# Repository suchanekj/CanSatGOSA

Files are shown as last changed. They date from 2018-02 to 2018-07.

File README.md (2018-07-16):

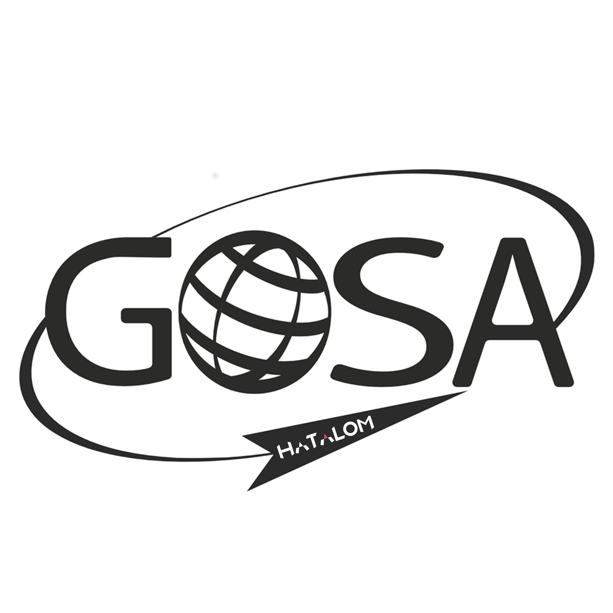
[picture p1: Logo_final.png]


# About
CanSat code is software for autonomous exploration and landings of probe "CanSat" developed by Gymnazium Opatov Space Agency especially by Jakub Suchánek.

The whole code is using following subcodes:
* GroundStation - incoming datas of pressure, position, time and temperature
* Cansat (2.0) - used libraries - Code, Cirtuits...
* Final report (Detail information about the probe Cansat in LaTex article. Unfortunately only in Czech.)
* Pre launch report - English detail description of Cansat 2.0
* Analysis - our own atmospheric model running on data from CanSat
* After flight report - final description of the whole project

# Support
In case you need help with use of our program or support us, you can contact us on our public email dotazy@gosa.cz or on email of programming director suchanek989@seznam.cz

# Contributing

Contributions are welcome and encouraged.  You can contribute in many ways:

* Documentation updates and corrections.
* How-To guides - received help? Help others!
* Bug reporting & fixes.
* New feature ideas & suggestions.

# Requirements
* Hardware requirements: qbcan for matching ports or an AVR microcontroller with RFM69HW (will have to edit port specifications)
* Idealy used for original construction of CanSat: https://github.com/suchanekj/CanSatGOSA/tree/master/Schematics
* Also used for original construction of CanSat 2.0: https://github.com/suchanekj/CanSatGOSA/tree/master/CanSat2.0/Schematics 
* Software requirements: AVR chip programmmer

# Used code
* Uses the RFM69 Library from: Feix Rusu (2014), felix@lowpowerlab.com http://lowpowerlab.com/
* Inspired by qbcan library and hardware http://doc.open-cosmos.com/Qbcan_modular

# Open Source / Contributors
CanSat software that is **open source** and is available free of charge without warranty to all users.

Current contributors:
* Suchánek, Jakub (suchanekj)
* Novotný, Patrik  (PatriktheAstronomer)
* Vítek, Martin (MArtytraM99)
* Zeman, Jakub (Jakubzmn)
* Völfl, Lukáš (LukasVolfl)
# Versions:
* 1.0 Groundstation subcode created and README added 29/03/2018
* 1.1 CanSat subcode created and Model files completed 01/04/2018
* 1.2 Final report (LaTex article) created 03/04/2018
* 1.3 Final report (LaTex article) completed 12/04/2018
* 2.0 New contributers, Analysis, CanSat 2.0 3D printed parts and PLR.pdf (Pre-launch report) added 18/06/2018
* 2.1 Analysis part 2 completed, chamber software added 28/06/2018
* 2.2 After flight report added, Analysis repaired and added - project completely done 16/07/2018
 (**Thanks everyone for your support to our project!**)

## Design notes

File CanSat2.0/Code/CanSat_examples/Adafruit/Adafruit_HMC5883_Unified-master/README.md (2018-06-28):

#Adafruit HMC5883L Driver (3-Axis Magnetometer) #

This driver is for the Adafruit HMC5883L Breakout (http://www.adafruit.com/products/1746), and is based on Adafruit's Unified Sensor Library (Adafruit_Sensor).

## About the HMC5883 ##

The HMC5883L is a digital (I2C) compass (magnetometer).  The magnetometer measure magnetic force, which is useful to detect magnetic north.

More information on the HMC5883L can be found in the datasheet: http://www.adafruit.com/datasheets/HMC5883L_3-Axis_Digital_Compass_IC.pdf

## What is the Adafruit Unified Sensor Library? ##

The Adafruit Unified Sensor Library (**Adafruit_Sensor**) provides a common interface and data type for any supported sensor.  It defines some basic information about the sensor (sensor limits, etc.), and returns standard SI units of a specific type and scale for each supported sensor type.

It provides a simple abstraction layer between your application and the actual sensor HW, allowing you to drop in any comparable sensor with only one or two lines of code to change in your project (essentially the constructor since the functions to read sensor data and get information about the sensor are defined in the base Adafruit_Sensor class).

This is imporant useful for two reasons:

1.) You can use the data right away because it's already converted to SI units that you understand and can compare, rather than meaningless values like 0..1023.

2.) Because SI units are standardised in the sensor library, you can also do quick sanity checks working with new sensors, or drop in any comparable sensor if you need better sensitivity or if a lower cost unit becomes available, etc. 

Light sensors will always report units in lux, gyroscopes will always report units in rad/s, etc. ... freeing you up to focus on the data, rather than digging through the datasheet to understand what the sensor's raw numbers really mean.

## About this Driver ##

Adafruit invests time and resources providing this open source code.  Please support Adafruit and open-source hardware by purchasing products from Adafruit!

Written by Kevin (KTOWN) Townsend for Adafruit Industries.

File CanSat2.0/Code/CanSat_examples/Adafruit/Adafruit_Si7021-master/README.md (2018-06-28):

Adafruit Si7021
===============

Driver for Adafruit's Si7021 humidity / temp sensor breakout

Designed specifically to work with the Si7021 breakout in the adafruit shop

   * https://www.adafruit.com/products/3251

This chip uses I2C to communicate, 2 pins are required to interface

Adafruit invests time and resources providing this open source code, 
please support Adafruit and open-source hardware by purchasing 
products from Adafruit!

Check out the links above for our tutorials and wiring diagrams 

Written by Limor Fried/Ladyada for Adafruit Industries.  
BSD license, all text above must be included in any redistribution

To download. click the ZIP button on the right, rename the uncompressed folder Adafruit_Si7021. Check that the Adafruit_Si7021 folder contains Adafruit_Si7021.cpp and Adafruit_Si7021.h

Place the Adafruit_Si7021 library folder your arduinosketchfolder/libraries/ folder. You may need to create the libraries subfolder if its your first library. Restart the IDE.

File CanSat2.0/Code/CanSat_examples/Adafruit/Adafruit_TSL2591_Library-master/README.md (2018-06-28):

# Adafruit TSL2591 Library 



This is an Arduino library for the TSL2591 digital luminosity (light) sensors. 

Pick one up at http://www.adafruit.com/products/1980

You'll also need the Adafruit_Sensor library from https://github.com/adafruit/Adafruit_Sensor

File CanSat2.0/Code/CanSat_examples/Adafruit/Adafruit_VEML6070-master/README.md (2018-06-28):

# Adafruit VEML6070 Library 



This is a library for the Adafruit VEML6070 UV sensor breakout:
  * https://www.adafruit.com/products/2899
 
Check out the links above for our tutorials and wiring diagrams. This chip uses I2C to communicate

Adafruit invests time and resources providing this open source code, please support Adafruit and open-source hardware by purchasing products from Adafruit!

Written by Limor Fried/Ladyada for Adafruit Industries.
MIT license, all text above must be included in any redistribution

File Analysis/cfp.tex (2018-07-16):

%Jak dělat reference:
% \cite{baker}

%Jak dělat poznámky:
% \footnote{tralala}

% TO DO
% Některá vysvětlení rovnic mohou být málo srozumitelná, chtělo by to víc se rozepsat (hlavně při úrovni pana grafa (který podle mě je fyzik mezi porotci))
% přidat pod rovnice popis proměných
% ohybani svetla vysvetlit, prepocitavani namerenych spektro hodnot taky, jeste absolute humidity

%
\documentclass{cfp}  

%
\usepackage[utf8]{inputenc}
\usepackage{chngcntr}
% \usepackage[margin=1in,includeheadfoot,headheight=13.6pt,footskip=2cm]{geometry}
\usepackage{amsmath}
\usepackage{pgfplots}
\usepackage{listingsutf8}
\usepackage{graphicx}
\usepackage{amsfonts}
\usepackage{txfonts}
\usepackage[colorlinks=true,urlcolor=blue]{hyperref}
\usepackage{eurosym}
\usepackage{chemfig}
\usepackage[version=4]{mhchem}
\usepackage{multicol}
\usepackage[symbol*]{footmisc}
\usepackage{indentfirst}
\usepackage{mathtools}
\usepackage{fixltx2e}
\usepackage{siunitx}
% \usepackage{titlesec}
% \usepackage{float}
% \usepackage{fancyhdr}
% \usepackage{array}
% \usepackage{longtable}
% \usepackage{dirtytalk}
\pdfminorversion=5 
\pdfcompresslevel=9
\pdfobjcompresslevel=2

\counterwithin{figure}{section}
\counterwithin{equation}{section}
\renewcommand{\thefootnote}{\fnsymbol{footnote}}
\setlength{\parindent}{3ex}
\setlength{\parskip}{0ex}
\newcommand{\rpm}{\sbox0{$1$}\sbox2{$\scriptstyle\pm$}
  \raise\dimexpr(\ht0-\ht2)/2\relax\box2 }
\newcommand{\degree}{^{\circ}}
\begin{document} 

   \title{CFP-18-Hatalom}

   \subtitle{ Simulation of finding life and life supporting conditions on exoplanets }

   \author{J. Suchánek
   		  \inst{1}
		  \and          
          P. Novotný
   		  \inst{2}
   		  \and
   		  J. Janoušek
   		  \inst{3}
   		  \and
   		  Lukáš Völfl
   		  \inst{4}
   		  \and
   		  Martin Vítek
   		  \inst{5}
   		  \and
   		  Jakub Zeman
   		  \inst{6}
          }
          
   \institute{Gymnázium Opatov, Czech Republic\\
              \email{suchanek989@seznam.cz}
         \and
             Gymnázium Opatov, Czech Republic\\
             \email{patrik.novotny.jes@seznam.cz}
         \and
             Gymnázium Opatov, Czech Republic\\
             \email{honza.janousek.11@gmail.com}
         \and
             Gymnázium Opatov, Czech Republic\\
             \email{luky.volfl@gmail.com}
         \and
             Gymnázium Opatov, Czech Republic\\
             \email{martulavitek@seznam.cz}
         \and
             Gymnázium Opatov, Czech Republic\\
             \email{kubazeman@volny.cz}
             }

   \date{July 15, 2018}

% \abstract{}{}{}{}{}
 
  \abstract
  % context heading (optional)
  % {} leave it empty if necessary  
   {Our analysis, like our mission, deals with the detection of life and the conditions necessary for its creation and development.}
  % aims heading (mandatory)
   {This work aims to introduce the analysis of the data we made after the flight of our Cansat and partly our entire project.}
  % methods heading (mandatory)
   {We conducted two types of analysis, biological analysis, and calculations of other variables using our own models that we developed. These are approximation models that are all available on our Git. This document also serves as their documentation.}
  % results heading (mandatory)
   {Tested planet seems habitable and even contains both microscopic and macroscopic life identical in basic structure to the life on Earth.}
  % conclusions heading (optional), leave it empty if necessary 
   {The analysis was thorough enough to declare with near certainty that it is habitable for humans. The project has had some failures but the analysis has turned out correct.}

   \keywords{Cansat, Gram's staining, Greenhouse effect, Exoplanet properties, Kepler 62, Atmospheric spectroscopy}

   \maketitle
%
%________________________________________________________________

\section{Introduction}
\par Our vision of Cansat was to build an interplanetary probe, which should not take care of the process of getting to a planet but the landing. We are landing at another planet. The one we selected is a planet orbiting around star named Kepler 62. It cannot be seen by an eye from Earth and its radius is smaller than radius of our Sun. Kepler 62 is situated in Lyra constellation and it is nearly 1,200 light years away from the Solar System. There are 5 planets orbiting around Kepler 62. Two of them, “e” and “f”, are very interesting for us as they lay in the habitable zone.
\par Planet “e” lies on the inner side of the habitable zone. According to calculations made using its semi-major axis, it is too hot for the possibility of existence of life similarly to Venus. However, its sibling Kepler 62f is much more promising. We do not have every piece of data, but we know that in the given orbital distance from the Kepler 62, the planet should have temperature of -40$^\circ$C. However, if it had 5 times thicker atmosphere composed of CO\textsubscript{2}, which is not anything uncommon, liquid water could be present on the surface of the planet. Kepler 62 is a stable star with low mass and metallicity compared to the Sun. It should shine twice as long than what is the age of the universe.
\par The whole system is up to 2 billion years older than our system. The planet probably has its own moon and an inclined rotational axis, therefore seasons change while orbiting its parent star. From all this data, we can assume that there is not any better candidate for finding extraterrestrial life. We can estimate lower stage of evolution according to the fact that we are not receiving any data transmission from the Kepler 62 system.
\par As the planet has thick atmosphere, controlled landing is possible. We have decided for drone-like landing with 4 rotors. Our aim is to land in a pre-determined spot, where our Cansat takes sample of the soil from the ground. Then we post-analyse the sample in our decontamination chamber which we had made ourselves.
\par Of course, it is necessary to realise that the whole mission was actually a simulation on Earth, so the expected outcome is whether we can prove that the Earth is habitable and inhabited and compare our measured and calculated data to the real ones to prove the functionality of our Cansat. However, some outputs are calculated also as on Kepler 62f.
\begin{figure}[!h]
\centering
\caption{Diagram showing the Kepler 62 system}
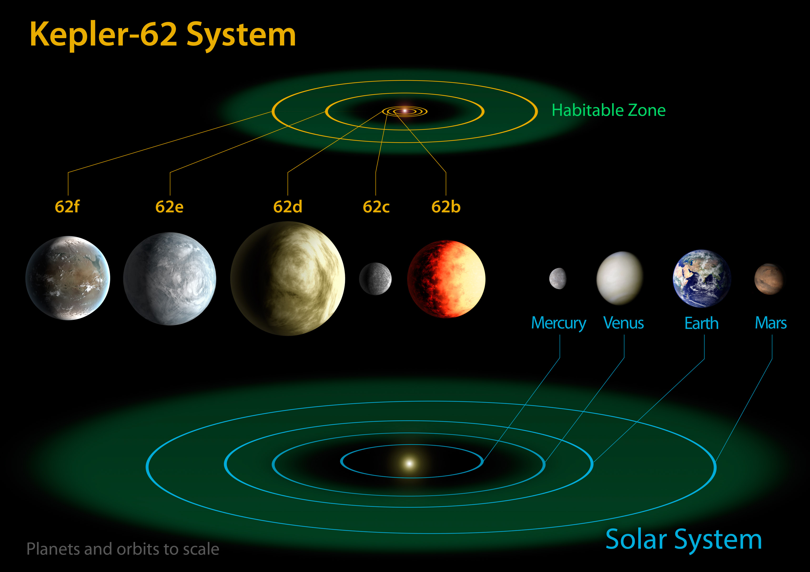
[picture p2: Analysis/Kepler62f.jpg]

\end{figure}
\section{Project description}
\par Our objective was to simulate a sample retrieval mission to a potentially habitable exoplanet, where a sample of soil is taken as well as a video and numerous data assessing the probability of Earth-like life existing on the planet.
\par The main goal was to detect life and conditions for it such as concentration of various gases. Those achievements are necessary for the launch to be considered successful. Other goals were to land the Cansat in a predefined location and to broadcast live data and video to our websites. \cite{Websites}
\par Our task was not easy and we have been aware of that since beginning of the project. We knew that not all of the parts will work but we were prepared for that. Our strategy was to fill as much as we could with sensors and other electronic devices so that in case of one sensors failure we would still get a lot of data to be processed. Unfortunately, before the final flight unexpected problems occurred and we did not have enough time to fix them. The most of hardware was working fine, however, because of few substantial mistakes our Cansat did not work at all. These issues and other information about construction are described in following paragraphs.
\subsection{Cansat}
\subsubsection{Materials and structural design}
\par The main structural body consists of 6 hull parts, which are 3D printed and is screwed to each other. The hull is round at the top and consists of four pillars in the remaining space. Four arms made out of carbon rod are attached to the top part in such way that they can easily move themselves into horizontal position. At the ends of the arms there are printed motor holders for secure and tight fit. In the pillars there are 16 batteries providing the whole Cansat with enough power for the flight and measurements.
\par The space inside was filled with various electronic parts. On the top, there is a three-part main circuit board, which is the “brain” of whole Cansat and on which most of sensors are placed. In the lower inside area there is a flight controller, a power regulator, a servo for soil sample and camera which broadcasts the whole flight to the ground station. All of these parts were  connected to a vertical PCB interconnecting everything and attaching it to the main PCB.
\par According to our plan GSM module should be sited near the flight controller for receiving other data. However, we are convinced that using GSM does not make any sense with our mission, landing on exoplanet.
\begin{figure}[!h]
\centering
\caption{Block diagram}
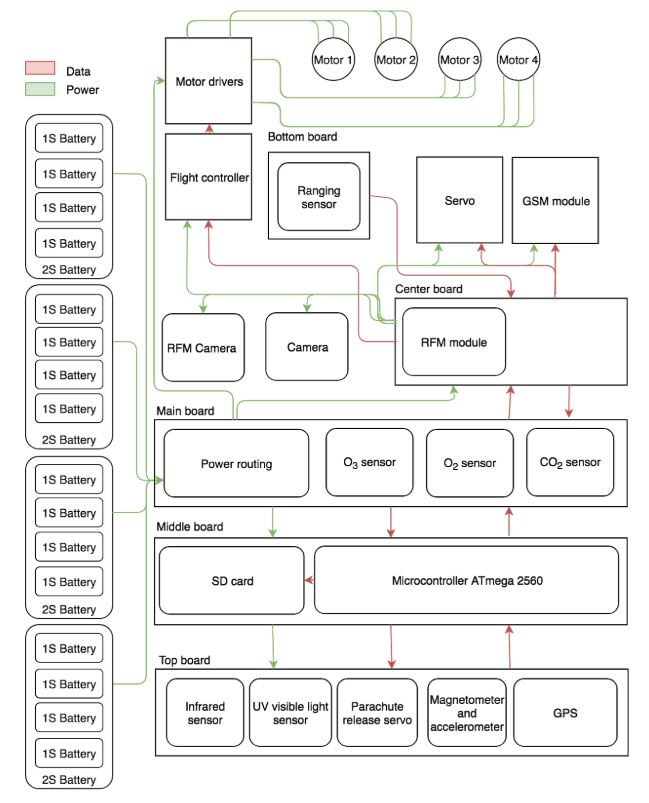
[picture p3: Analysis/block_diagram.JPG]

\end{figure}
\subsubsection{The main hardware issues}
\par During construction and testing of our Cansat there kept repeatedly occurring severe issues with I2C interface devices. The fact that all these problems always disappeared spontaneously made them very difficult to diagnose and we were not able to detect the main reasons of the occasional misbehaviour of our Cansat. All these led to the critical moment, when, despite many successful tests, the SPI and I2C interfaces stopped responding a few moments before the final launch. Due to this, we lost, among the others, also sensors (connected to I2C) measuring the altitude, velocity, acceleration and proximity, which were necessary for the autonomous drone landing system. Secondly, despite values from analogue sensors still being measured, we were unable to store or transmit any data because of not working transmitter and SD card (connected to SPI). 
\par Despite precise tests and measurements after the launch, such as connecting every single sensor separately to the Arduino and checking it or searching for any possible shorts, we could not identify the concrete issue.
\par The most probable explanation is a short between mentioned interfaces which was caused by a metal fragment from cutting PCBs or a thin piece of wire fallen in the circuit. This theory is also supported by the fact that there were found a few metal fragments in drone motors.
\par According to mentioned information, the main reason is in general the insufficient precision during the manipulation with Cansat and avoiding impurities.
\subsubsection{Recovery system}
\par The descent should have been controlled using 4 electric motors which combined have about 640 g of thrust at max. We had planned that arms holding the motors put themselves from resting position into flight position. This system was tested three months before the final competition with receiver placed in Cansat, which was connected to transmitter controlled by a person. The test was successful and Cansat was able to fly with someone’s help. 
\par The stabilisation was possible thanks to flight controller F3 SP Racing, which is normally used as a main board for racing quads. It contains only an accelerometer, gyroscope and tuned software needed for communication with ESCs (Electric speed controller). All of these parts, motors as well, were made for quad racing and for this reason our satellite had enough power and a fast response.
\par After stabilisation motors should have slowed down the descent and then it would have been navigated by GPS, barometer for precise height and magnetometer. Right above ground, about 5 meters, Cansat would have slowed down even more for soft touchdown.
\par Before flight we were forced to use parachute only because of the problems mentioned above. For some reason GPS became very unreliable since we landed on Azores. From our point of view, it could be damaged during flight to Azores or during checking our luggage in. After the issues with  I2C interface the other important sensors like accelerometer and proximity sensor became non-functional. Without all these sensors we were unable to determine the exact location of our Cansat and flight with propellers was impossible.
\begin{figure}[!h]
\centering
\caption{Exploded view}
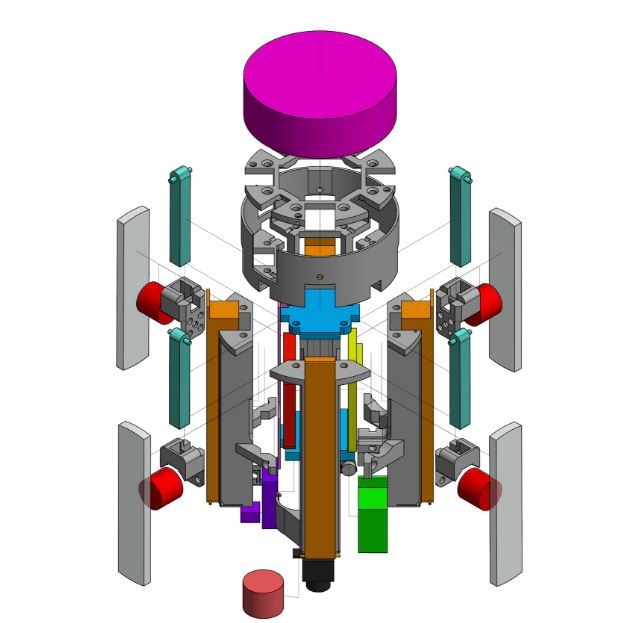
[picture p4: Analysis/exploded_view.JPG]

\end{figure}
\subsubsection{Double emergency landing system}
\par What we would like to highlight is our solution of the emergency landing. To explain our emergency system it is necessary to mention, that the logics based on ATmega and the flight-controller are two separated systems, so that any error on one of them can’t influence the other one. 
\par In case of failure of any “drone part”, such as motors, regulator or already mentioned flight-controller, the logics detect this misbehaviour (e.g. to high descend velocity), it stops the motors and releases the parachute using a small servo placed near the top board. After that the Cansat would be able to land safely. That is how our primary emergency system works.
\par The secondary emergency landing system is activated when the logics stops working. In this case the flight-controller overtakes the control of motors, sets a stable throttle for slow descending and lands, using its own embedded gyroscope.
\subsubsection{Final electrical design}
\par The CanSat contained nine custom PCBs. In the top part three parallel round PCBs were located. The top one contained sensors:
\paragraph{GPS ublox neo-m8n}This  module contains two independent parts: compass, which communicates via I2C and GPS module connected to serial port. It has also its own memory to store the last recognised location, so it can synchronise faster when initiated. It is very important sensor for autonomous landing.
\paragraph{Humidity sensor SI7021}Humidity is important factor when investigating the possibility of life. Using I2C inteface. Its precision is $\pm$ 3$\%$ RH (max), 0–80$\%$ RH
\paragraph{Light sensors TSL25911 (visible and infrared)}From observing received light in different altitudes is possible to estimate content of the atmosphere. Using I2C interface.
\paragraph{VEML6070 (ultraviolet)}UV light is dangerous for many forms of life and its measuring in different altitudes give us a chance to estimate content of the atmosphere. Using I2C interface.
\paragraph{Pressure and temperature sensor MPL3115}Combined with other data (e.g. G), pressure can be used to count the thickness of the atmosphere and the right temperature is necessary for planet’s habitability. Using I2C interface. Precision ADC resulting in 0.1 meter of effective resolution.
\paragraph{Magnetometer and accelerometer LSM303AGRTR}This sensor is essential for the autonomous landing system. Using I2C interface.
\par On the middle board there were an ATmega2560 microcontroller and a SD card. The lower board took care of power routing and regulation and also contained gas sensors:
\paragraph{MG812 (CO\textsubscript{2})}Range: 350-10000ppm CO\textsubscript{2}
\paragraph{MEO2 (O\textsubscript{2})}Range: 0-25\%vol
\paragraph{SP3-61 (O\textsubscript{3})}Range: 100ppb O\textsubscript{3}
\par Levels of these three gasses are very important when investigating the habitability of the planet, especially for atmosphere’s breathability and the greenhouse effect. Then our Cansat was equipped  with one external sensor:
\paragraph{Distance laser sensor VL53L0X}This sensor helps with soft touchdown of Cansat, because GPS and barometer are not accurate enough. Using I2C interface.
\par Batteries were connected four in parallel on each pillar PCB which have connectors for charging and connection. To the bottom of the main PCBs was connected a vertical PCB to which all modules or devices were connected. In that space motor drivers, flight controller, gamma detection board, sample collection servo, and camera were located.
\par Sixteen 1S LiPo batteries are used in a 2S (7.4V) configuration. Each battery gives 200 mAh at 3.7V and allows 35C discharge. That amounts to 1600mAh at 7.4V and 280C discharge. All logic electronics had been expected to draw up to 1A and the motors draw 15A on average. Because we decided to use only parachute we had much more energy than we had supposed. After the flight the voltage of one battery cell was at 4,1 V (maximum charge is 4,2 V). 
\par The PCBs were designed using KiCAD. All schematics are available at our GitHub/../Circuit \cite{Git-Circuit} and a detailed list of parts is located at our website. \cite{Websites}
\subsubsection{Sofware design}
\par The program initializes and then keeps running in loop where it measures data from sensors and GPS, based on GPS controls motors speed and CanSat’s direction and transmits data to ground station.
\par If any component fails, a watchdog is triggered to reset the microcontroller and the faulty component is disabled during initialization. If this happens during flight or any component required for flight is disabled the program jumps to parachute flight as a security precaution, disabling the motors and releasing the parachute. This happens within five seconds of a fault causing the program to freeze.
\par All Cansat software is written in Arduino code based on C++. We used a huge amount of libraries for which we thank their creators. We used CLion IDE, Atom editor, Arduino IDE and PDE (Processing Development Environment). Every bit of our code or code we used has GNU GPL license and it is available at our GitHub. \cite{Git - Code}
\begin{figure}[!h]
\centering
\caption{Software decision tree}
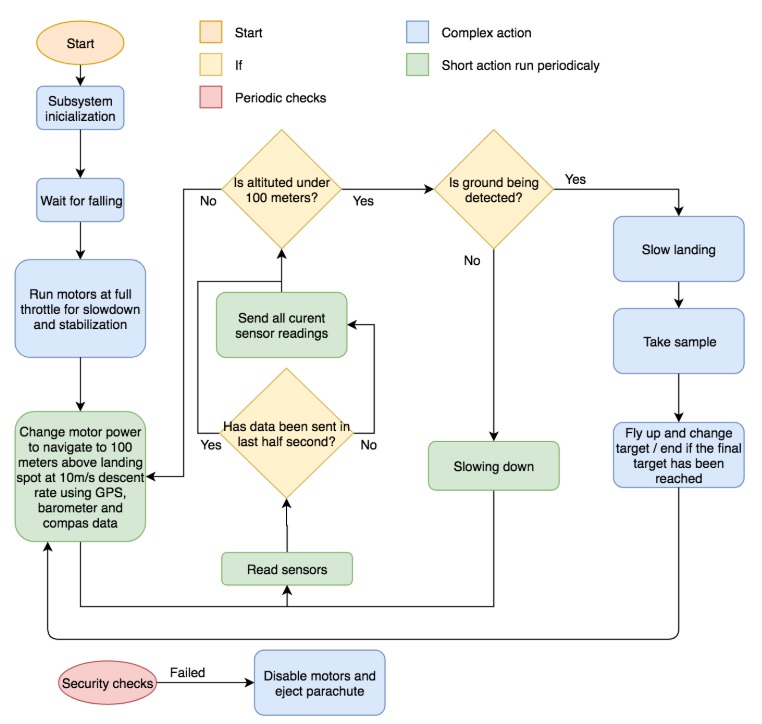
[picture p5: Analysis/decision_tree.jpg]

\end{figure}
\subsection{Ground station}
\subsubsection{Ground support equipment}
\par The ground station is split up between two laptops. One is receiving through an analogue antenna the video feed from onboard camera. The emitting power of video transmitter was approximately 200 mW and for two kilometers we needed more. However, we were limited by space in our satellite and by maximum power of batteries. For this reason, we decided to use diversity receiver with three patch antennas (14 DBI). That set should work to distance over 2,5 km. The receiving video was saved locally on the computer. We had also planned to stream the video to our Youtube channel for fans but there was no stable internet connection on the spot of the flight. 
\par The second laptop was connected to Arduino Nano via USB connection and runs a processing sketch which listened to Arduino’s serial. The sketch processes the input data, saves all communication and logs errors were capable of sending data to our web page where it is stored as a backup and graphed for live inspection. The Arduino is running a simple script for receiving data from Yagi antenna which we made ourselves and printing it to the serial.
\section{Data measurements and processing}
\subsection{Theory}
\subsubsection{Basic variables}
\paragraph{Gravitational acceleration}If we average each partial acceleration measured and calculate a Pythagorean sum of those, we should get gravitational acceleration. The problem is that the axis can not rotate during measurements. The data from a gyroscope is not reliable enough due to low sampling level. Therefore only data measured on the ground can be used.
\paragraph{Atmospheric density} The vertical gradient of pressure is linear to the density of the air:\\
\begin{equation}
    \rho = g \frac{dp}{dh}
\end{equation}
\paragraph{Atmospheric composition} \label{basic}
From Tinetti's analysis \cite{Tinetti} we obtained the general composition of the exoplanet atmosphere, depending on the variables we know or can compute:
\begin{figure}[!h]
\centering
\caption{Exoplanet composition}
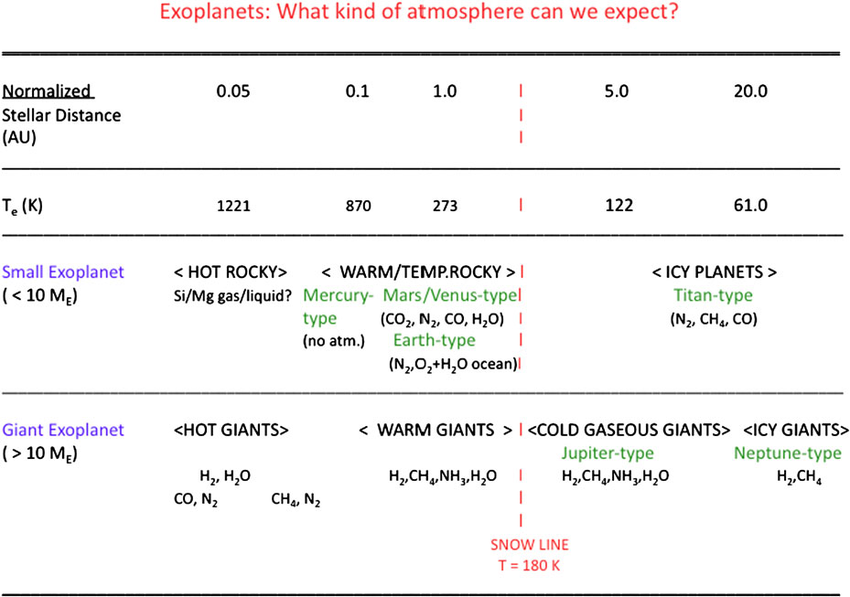
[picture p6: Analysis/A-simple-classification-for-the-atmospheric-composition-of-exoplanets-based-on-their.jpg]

\end{figure}
\paragraph{Mass of the planet} The mass of the planet can be obtained using Newton's law of gravity:\\
\begin{equation}
    M = \frac{g R^2}{G}
\end{equation}
\paragraph{Atmospheric density} The vertical gradient of pressure is linear to the density of the air:\\
\begin{equation}
    \rho = g \frac{dp}{dh}
\end{equation}
\paragraph{Average molecule mass} We can derive the number of particles per unit of volume from the ideal gas law and from that and density the molecule mass:\\
\begin{equation}
m_{molecule} = \frac{\rho}{N} = \frac{\rho k_B \tau}{p}
\end{equation}
\paragraph{Mass of the atmosphere}
From Trenberth's analysis \cite{Trenberth} we get an equation to calculate the mass of atmosphere:
\begin{equation}
m_{atm} = \frac{2\pi R^2 f}{g} \int_{-\frac{\pi}{2}}^{\frac{\pi}{2}} [p_s(\theta)]cos\theta d\theta
\end{equation}
where $f$ is the net effect of the shape of the planet and gravity variations with height and latitude but its value is very close to one and therefore at our level of precision negligible, as we cannot determine it exactly, $R$ is radius of the planet, $g$ is gravitational acceleration and $[p_s]$ is the average surface pressure. \subsubsection{Size of the atmosphere}
The two major factors limiting the size of the atmosphere, that is the altitude, at which an average molecule will escape into space, are the following:
\paragraph{Speed of molecules exceeding escape velocity} Even the top of the atmosphere rotates with the planet so the speed of some molecules is at least the sum of the rotational velocity and mean quadratic velocity of the molecules. As the velocity of molecules depends on temperature, which we did not measure a guess must be made. As there is very low density at the top of the atmosphere, the thermal conductivity can neglected. The top of the atmosphere is mostly heated by highly energetic particles from deep space (they do not originate in the star so their concentration can be considered constant in nearby stellar systems. Therefore we can say the temperature there is the same as at the top of the atmosphere of the Earth with the expected precision of a 100 kelvins (it propagates only as a small deviation).
\paragraph{Magnetosphere} We can expect form figure \ref{mag} and from Maxwell's second equation that the size of magnetosphere will be roughly linear with size and from the figure that a magnetic field at least third of the size of Earth's one will be good enough.
\begin{figure}[!h]
\centering
\caption{Earth magnetosphere under solar wind pressure}
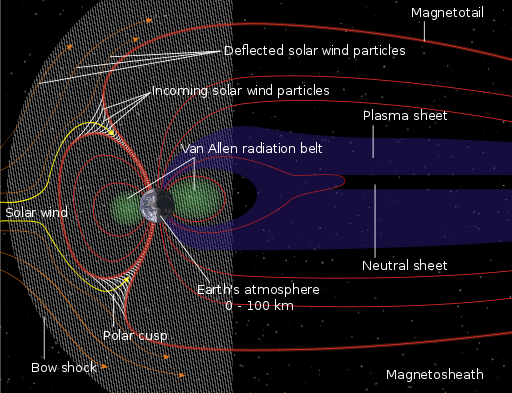
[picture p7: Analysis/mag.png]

\label{mag}
\end{figure}
\begin{align}
v_{escape} &= v_{rotational} + v_{mean quadratic}\\
\sqrt{\frac{2MG}{r}} &= \frac{2 \pi r}{T_{rotation of planet}} + \sqrt{\frac{3 k_B \tau}{m_{molecule}}}
\end{align}
\paragraph{Solar constant}
\begin{align}
P = \frac{k_B*4*\phi*r_{star}^2*T_{star}^4}{d^2*4*\phi}
\end{align}
where $k_B$ is Boltzmann's constant, $r_star$ is Parent star's radius, $T_star$ represents parent star's surface temperature in kelvins, d represents distance between the star and the place, where we measure solar constant. Basically, it is the radiance of an absolutely black body on an area of 1 $m^2$ per sphere of a given radius.
\paragraph{Temperature without greenhouse effect}
\begin{align}
T = \bigg(\frac{P}{4*k_B} * (1-A)\bigg)^{0.25}
\end{align}
where A is albedo, which is the variable that tells us what amount of light on a scale from 0 to 1 reflects the body. The rest variables and constants were mentioned above. 
The resulting temperature will be in kelvin of course.
\subsubsection{Greenhouse effect}
\par This is a very complex issue, first it is necessary to calculate spherical variables depending on the position on Earth and time. We then move on to more complex purely physical calculations.
\par First, we calculate when the sun passes through the local meridian.
\begin{align}
t_{noon} = 12 + t_{delta} + \frac{\lambda+Z*15}{15}\\
\end{align}
\par where $t_{delta}$ represents the changes made by the law as summer or winter time, at Azores it was +1, then $\lambda$ is longitude value. And Z represents time zone, Azores belong to UTC time zone. The whole idea is that the Earth rotates about 24 hours around its axis (360 degrees). Thus, the angular distance from the meridian that defines the time zone can also be considered as a time distance. 
\par Changes in the angle of the bodies in the sky in the horizontal direction are linear, as it is based on the rotational speed of the Earth, which is constant. We will use this fact in further calculations. These inconsistencies can usually be neglected, but the time zone of Azores does not correspond to its geographical location, and therefore it is necessary to consider this matter and calculate when the astronomical noon is taking place. It is then necessary to compute the maximal declination which is the key for us, in addition it provides an important fact how long does it last between the sunrise and sunset.
\begin{align}
\delta = 23.45*\sin(0,98*DD+29,7*MM-109)
\end{align}
DD represents the day of the month and the MM month of the year. Since the earth axis performs precision and nodding movement, our calculations are based on an approximation according to our national standard ČSN 730581.
\begin{align}
\delta_{max} = 90-\phi+\delta
\end{align}
where $phi$ is latitude. This relationship gives us a maximum declination on a given day at a given place on the ground. This is derived from the basic trigonometry. Then we can calculate length of the day, our calculations are based on the Giesen's \cite{Giesen}.
\begin{align}
t_{rise} = 12 - \frac{arccos(-\tan(\phi)*\tan(\delta))}{15} \\
t_{set} = 12 + \frac{arccos(-\tan(\phi)*\tan(\delta))}{15}\\
t_{daylight} = \frac{2*arccos(-\tan(\phi)*\tan(\delta))}{15}
\end{align}
where $t_{rise}$ is a time of sunrise, $t_{set}$ time of sunset and $t_{daylight}$ represents length of the day. 
Now we can calculate how much energy a $m^2$ has taken over the time from sunrise to measurement time.
\begin{align}
\delta_{time} =\frac{\delta_{max}}{t_{noon}-t_{rise}}*(t-t_{noon})
\end{align}
or (for measurement after real noon)
\begin{align}
\delta_{time} =\frac{\delta_{max}}{t_{set}-t_{noon}}*(t_{set}-t)
\end{align}
where t is current time of measurement. As it was mentioned above, the angular velocity is linear, so the height of the Sun is determined for some time as the ratio of the time elapsed versus the total time. Surface receives energy based on sine function:
\begin{align}
E =(1-A)*P*3600*(t-t_{rise}) \int_{0}^{\delta_{time}} \sin(x)
\end{align}
or (for measurement after real noon)
\begin{align}
E =(1-A)*P*3600*(t_{set}-t) \int_{0}^{\delta_{time}} \sin(x)
\end{align}
where A is albedo and P is so called solar constant, both is used and explained above in 3.9 and 3.10. Integral solution is: 
\begin{align}
\int_{0}^{\delta_{time}} \sin(x) = \cos(0) - \cos(\delta_{time})
\end{align}
if we have received energy on $m_2$, so we can calculate how this energy changed ground temperature.
\begin{align}
t_{ground} =t_{air} - \int_{a}^{b} \cfrac{1}{\frac{E*(1-A_{clouds})}{\rho*c}}
\end{align}
where $\rho$ is density of the ground, c is specific heat capacity, both of these values for final calculation are drawn from TBZ catalogue \cite{TBZ}. $t_{air}$ represents temperature measured at the ground level, $t_{ground}$ is our calculation of the temperature of the ground without heating by the parent star. $A_{clouds}$ is a number of albedo style (from 0 to 1), which represents how much energy from the sun the cloud reflects on his way to the surface. We have to think that the day when it is measured can be overcome. Cloud rate estimation can be determined from both our spectrographic analysis and the camera that the satellite carries. Consideration of this factor significantly improves the analysis. Taking into account the state of the sky on the day of the final flight and the work of Sigmund Fritz \cite{Fritz}, we consider albedo of the clouds in the final calculation as 0.55. Integral solution is:
\begin{align}
t_{ground} =t_{air} - \frac{1}{\frac{E*(1-A_{clouds})}{\rho*c}}*\frac{\ln{b}-\ln{a}}{b-a}
\end{align}
by using the integral and dividing the boundaries we get an average value. Here, it is necessary to realise what the integral means. From the hyperbolic function (it is logical that with the depth the average value will be closer to the air temperature, if we neglect the lower heating of the soil, it is the passage of the energy from the top layer below, respectively in the winter this phenomenon works on the contrary) we obtained the difference of logarithms, zero argument can not be inserted into the logarithm. Why is that so? The boundaries determine the area of the soil, which according to us is warming up and the average tells us then how this area is heated as a whole. Therefore, the soil layer logically can not have zero value, here mathematics and physics are beautifully interconnected. We have therefore chosen a range of 12 to 90 centimetres.
(Our model is available online so you can play with the limits according to your preference.)
\begin{align}
a = 0.12
\end{align}
\begin{align}
b = 0.9
\end{align}
these limits are bounded by stable soil profiles B and C, whose temperature changes with respect to weather, but the change takes more time. This is a good representation of what we are looking for.
\begin{figure}[!h]
\centering
\caption{Soil types taken from work of Tapas Bhattacharyya \cite{Bhattacharyya}}
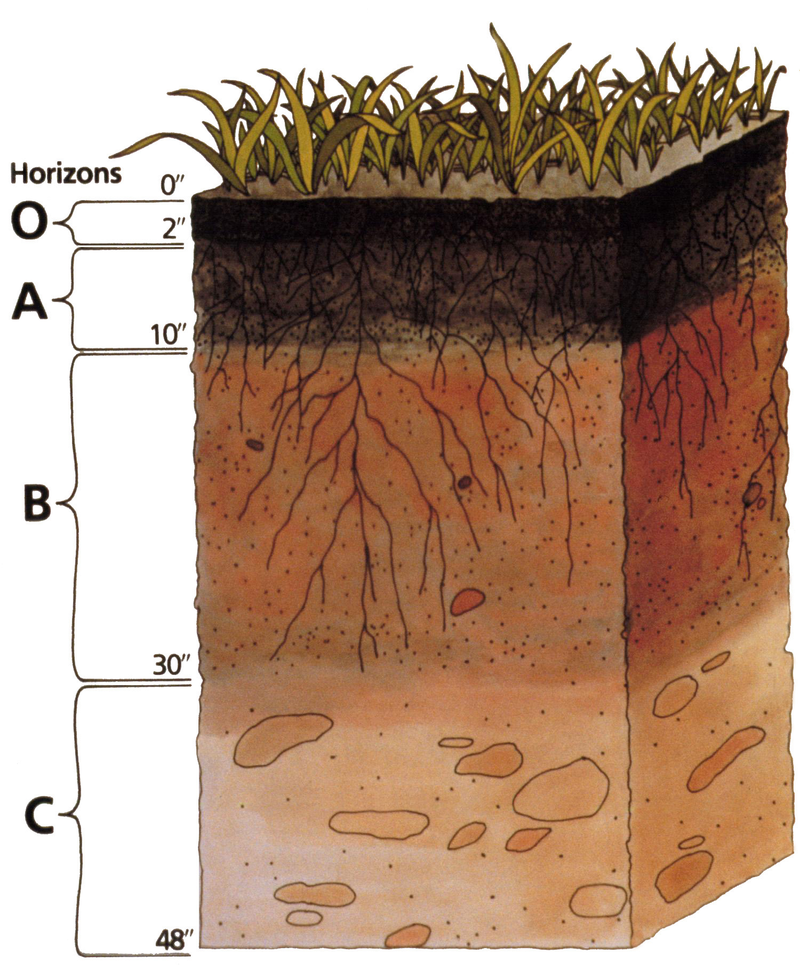
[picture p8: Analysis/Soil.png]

\end{figure}
\par Now we have the soil temperature, useful fact itself, but mainly essential for the final calculation of the greenhouse effect. We use this fundamental equation, which represents energy changes in the atmosphere, based on the greenhouse effect scripts from Harvard \cite{Jacob}:
\begin{align}
\phi*r_{planet}^2*P*(1-A) = \\ 4*\phi*r_{planet}^2*(1-f)*\sigma*T_{ground}^4 + 4*\phi*r_{planet}^2*f*\sigma*T_{air}^4
\end{align}
where A is albedo, P is solar constant. Both was used above. $\sigma$ represents Stefan-Bolzmann constant, $r_{planet}$ is a radius of the planet. From this equation we were able to compute f, which expresses the amount of reflected (longwave) radiation by the clouds back on the ground:
\begin{align}
 f = 2*(1-\frac{P*(1-A)}{4*\sigma*T_ground^4}
\end{align}
like the scripts we used formula for a separate energy balance equation applies to the atmospheric layer:
\begin{align}
f*\sigma*T_{ground}^4 = 2*f*\sigma*T_{air}^4
\end{align}
however they used system of equations differently. The value f is measurable on the global scale and nobody discovers it and uses this calculation to calculate the soil temperature. However, the temperature of the soil has been determined from the calculation by another method and thus we can very precisely determine the value of f, which is not very common. In other words, local measurement allowed us to have a variable valid for the entire planet.\par
\begin{figure}[!h]
\centering
\caption{Energy changes according to the scripts of Harvard}\cite{Jacob}
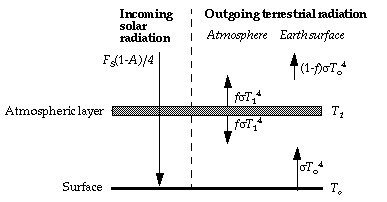
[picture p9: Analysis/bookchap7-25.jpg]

\end{figure}
As a final result of these all calculations we know f, however to get this result we need to derive a lot of variables that also provide us with interesting data - such as a square meter energy flow, which is important information for using solar panels as well as an estimate of the nature of life on the planet.
\paragraph{CO\textsubscript{2} equivalents}
\par The effect of a given gas on the greenhouse effect can easily be expressed in terms of carbon dioxide. Given this significance and the concentration of gas as a weighted average, it is possible to determine the extent to which the gas participates in the whole process. The only unknown is water vapour whose volume in the air is constantly fluctuating, but global warming is a global phenomenon \cite{Geocraft}, so we compared the state without steam, and then its coefficient was 0.72 in order to distort the results as little as possible other gases. However, the results without water vapour calculations are certainly reported and conclusive. According to Strobel, the coefficients are as follows \cite{Strobel}:
 \begin{tabbing}
    Gas ~~~~\= CO\textsubscript{2} equivalent ~~~~
    \= 34 \kill
    \bfseries  Gas\>\>
    \bfseries CO\textsubscript{2} equivalent\>\\
    $CO_2$ \>\>1.0\\
    $H_2O$ (vapour) \>\>0.72\\
    $CH_4$ \>\>80\\
    $O_3$ \>\>1000\\
    $NO_2$ \>\>300\\
    \end{tabbing}
\par It should be noted that the tropospheric ozone equivalent is 1000 units of $CO_2$, but due to the short lifetime, the value on the 20-year scale is only 62 to 69 units. \cite{Ozone co2e} We decided to use 1000 units for our calculations, so results represents properties of the atmosphere are exactly at the moment of measurement.
\subsubsection{Spectroscopic measurements}
We are using spectroscopic sensors with sensitivity functions depicted in Appendix 2. The theory often deals only with wavelengths 280-890 depicted there.
\paragraph{Thermal radiation at the top of the atmosphere} The spectral radiance is specified using Planck's law. As spectral radiance is radiant flux per wavelength per steradian, we can multiply it with the solid angular size of the star to calculate the spectral radiant flux at the ground if there were no atmosphere.
\begin{align}
\Phi_{e}(\lambda) &= B_{\lambda}(\lambda) \Omega_{Star}\\
\Phi_{e}(\lambda) &= \frac{2 hc^2}{\lambda^5}\frac{1}{ e^{\frac{hc}{\lambda kT}}-1} 4 \frac{\pi R_{star}^2}{4 \pi r_{planetary orbit}^2}\\
\end{align}
\paragraph{Luminous flux} Luminous flux is what the sensors measure. To do the analysis, first we have to calculate what they should measure if there were no atmosphere:
\begin{equation}
\Phi_v = 683.002 \frac{lm}{W} \int^{\infty}_0 \overline{y}(\lambda) \Phi_{e,\lambda}(\lambda)\, d \lambda
\end{equation}
where $\overline{y}$ is luminosity function.
\paragraph{Absorption} For every gas there is a function of wavelength that gives absorption cross section. Then we can calculate the absorbed portion of light at that wavelength.
\begin{align}
\frac{dN}{N} &= -dx n \sigma\\
N(\lambda) &= N_0(\lambda) e^{ -x \sigma(\lambda)}
\end{align}
Where $n$ is number of absorbing particles per unit volume and $N(\lambda)$ is the number of photons with wavelength $\lambda$. We can do the same for radiant flux:
\begin{align}
\Phi_{e} &= \Phi_{e0}(\lambda) e^{ -x \sigma(\lambda)}
\end{align}
If we set $n$ as particles per unit volume (cubic meter in SI) at sea-level (we use values from Earth because this is just for comparison), than $x$ would be the height of the layer of gas if it were pure and at sea-level. That is useful for comparison as for example ozone layer thickness is often given as such variable. It will be useful to determine the total masses of the gases. To do that we will suppose that composition of atmosphere is constant with height. We will also use the isothermic model for the atmosphere, because although it adds extra air in comparison with other models, there is air practically orbiting the planet (for Earth that is the case for the exosphere) which is ignored in the models based on the derivative of pressure. We need that to determine the mean spherical surface of the atmosphere. We can use barometric formula as density of air is linear to pressure for isothermic atmosphere.
\begin{align}
m_{gas} &= x_{gas} \rho_{gas} \frac{\int_R^\infty 4 \pi r^2 P_0 e^\frac{-g M (r - R)}{R^* T_b}}{\int_R^\infty P_0 e^\frac{-g M (r - R)}{R^* T_b}}\\
m_{gas} &= x_{gas} \rho_{gas} 4 \pi \Bigg(R \bigg(R + 2\frac{R^*T_b}{gM}\bigg) + 2\bigg(\frac{R^*T_b}{gM}\bigg)^2\Bigg) %vychází 8.9 km vysoko
\end{align}
where $\rho_{gas}$ is density of the gas at sea-level on Earth, it has to be on Earth because the thickness of the layer ($x$) is also a value converted to on-Earth.
\subsubsection{Overall concentration of gases in the atmosphere}
We can choose a few expected gases and determine their concentrations by fitting the calculated data (expected measurements with given concentrations) to the measured. We must also take into account the greenhouse effect and the mass of the atmosphere (the calculated amounts of gas from spectroscopy must add up to the mass of atmosphere).
\subsubsection{Sensor correction}
The sensors measure with decreased sensitivity when light is at an angle, also less light falls on the clouds, we have to calculate for this by dividing the measurement by sine of the angular height of sun above horizon. Near sunset and sunrise this has to be correlated by (arcminutes that have to bee added to the angle above horizon) \cite{refra}:
\begin{equation}
    R = 1.02 \cot \bigg( h + \frac{10.3}{h + 5.11} \bigg) \frac{p}{101} \frac{283}{273 + T}
\end{equation}
\subsection{Transmissivity of clouds}

\

We will try to estimate what proportion of light goes through cloud and what proportion is reflected. Every cloud is composed of big number of water droplets with average radius between $10 \mu m$ and $20 \mu m$. This radius is big in comparison with wavelengths of UV, visible light and IR so we cannot use Reyleigh approximation but we can use geometrical approach. 

\

Water droplet has a radius $R$ and the light has irradiance $E_{e}$.  We shall count refraction and reflection of light on the spherical droplet. Light enters the droplet in distance $r$ from the droplet axis as we can see it in the figure~1.

\begin{figure}[h]
\centering
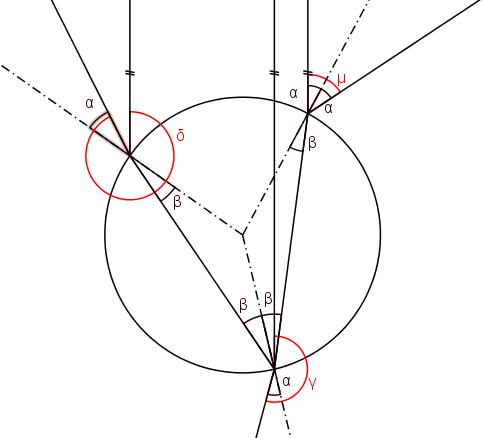
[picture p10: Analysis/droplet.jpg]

\caption{Light in a droplet}
\end{figure}

The angle of reflection is the same as the angle of incidence according to \textit{the law of reflection}, for angle of refraction holds the \textit{Snell's law}. One part of light is reflected and the rest is refracted. The ratio between these parts is described by \textit{Fresnel equations}. Light striking the droplet is randomly polarized so we can resolve it into two equally big components with $s$ and $p$ polarizations. The Fresnel equations are:
$$A_{s}={\left(\frac{\sin{(\alpha-\beta)}}{\sin{(\alpha+\beta)}}\right)}^2$$
$$A_{p}={\left(\frac{\tan{(\alpha-\beta)}}{\tan{(\alpha+\beta)}}\right)}^2$$
$R_{s}$ and $R_{p}$ denote fraction of power of reflected light in respective polarizations, $\alpha$ angle of incidence (which is the same as angle of reflection) and $\beta$ angle of refraction. Fractions of refracted light obviously are
$$B_{s}=1-{\left(\frac{\sin{(\alpha-\beta)}}{\sin{(\alpha+\beta)}}\right)}^2$$
$$B_{p}=1-{\left(\frac{\tan{(\alpha-\beta)}}{\tan{(\alpha+\beta)}}\right)}^2$$
In figure 1 we can see path of light with marked angles of incidence, reflection and refraction. The light is reflected and refracted infinite number of times, but from practical reasons we can take into account only three refractions and reflections (in simulation it turns out that almost 99\% of light exit the droplet during these three refractions and reflections).
We made a simulation using Microsoft Excel. For each distance $r$ from droplet axis (with certain step), we counted the dependence of radiant flux on angle under which the light exit the droplet and after counting for $r\in\left( -R, R\right) $ where $R$ is radius of droplet we obtained the function of radiant flux
$$\Phi_{e}(r, \mu, \gamma, \delta)$$
where $\mu$, $\gamma$ and $\delta$ are the angles under which the light exit the droplet after first, second and third reflection (refraction).

\begin{figure}[!h]
\centering
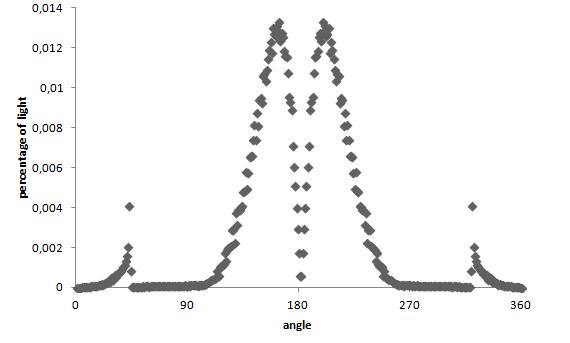
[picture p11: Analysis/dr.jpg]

\caption{Light in a droplet}
\end{figure}

We simplified this model and counted only the percentage of light which exit the droplet under angle between $(0^{\circ},90^{\circ})\cup(270^{\circ},360^{\circ})$ so it exit upwards and percentage of light which passes through droplet downwards under angle between $(90^{\circ},270^{\circ})$.
Our numerical simulation says, that the percentage of transmitted light is
$$\tau\cong94.8\%$$
This number does not depend on wavelength of light and not even on radius of the droplet.

\

How many droplets will the light ray hit after entering the cloud from above? As we can see in figure 2 the direction of the light ray after going through the droplet does not differ very much from original direction (maximum of light is refracted under 20$^{\circ}$). Thus, we can assume that the ray hits only droplets which are above each other. Each droplet transmits 94.8\% of light and 5.2\% is reflected. There are $n$ layers of droplets in one cloud. This system is in principle the same as the system of one-way mirrors. 

Let us consider two one-way mirrors. Incident ray has the intensity $I$. The transmissivity of both mirrors is $\tau$. Thus the part of light which passes through two one-way mirrors system is $\tau^2 I$. On the second mirror, $\tau(1-\tau) I$ is reflected. Then from the first mirror $\tau(1-\tau)^2 I$ is reflected and through the second mirror passes $\tau^2(1-\tau)^2 I$. We can see a sequence: $\tau^2 I$, $\tau^2(1-\tau)^2 I$, $\tau^2(1-\tau)^4 I$ ... The sum of this infinite sequence divided by $I$ is the transmissivity.
$$\Theta=\tau^2+\tau^2(1-\tau)^2+\tau^2(1-\tau)^4+\cdots=\frac{\tau^2}{1-(1-\tau)^2}=\frac{\tau}{2-\tau}$$
Now let us count the system of n one-way mirrors. Let the transmissivity of $n-1$ mirror be $\Theta$, then for the part of light which passes through $n$ mirrors holds (only slightly different from previous case):
$$T=\Theta\tau+\Theta\tau(1-\Theta)(1-\tau)+\Theta\tau(1-\Theta)^2(1-\tau)^2+\cdots=\frac{\Theta\tau}{1-(1-\Theta)(1-\tau)}=\frac{1}{\frac{1}{\Theta}+\frac{1}{\tau}-1}=\frac{1}{\frac{1}{\Theta}+\frac{1-\tau}{\tau}}$$
Using induction:
$$T_1=\frac{1}{\frac{1}{\tau}+\frac{1-\tau}{\tau}}$$
$$T_2=\frac{1}{\frac{1}{\tau}+\frac{1-\tau}{\tau}+\frac{1-\tau}{\tau}}$$
$$T_3=\frac{1}{\frac{1}{\tau}+\frac{1-\tau}{\tau}+\frac{1-\tau}{\tau}+\frac{1-\tau}{\tau}}$$
$$T_n=\frac{1}{\frac{1}{\tau}+n\frac{1-\tau}{\tau}}$$

System of $n$ one-way mirrors has the transmissivity
$$T=\frac{\tau}{n-\left( n-1\right) \tau}$$

\

Let us count number of layers $n$ for real situation and then make a comparison of our case with real number of layers.
There are $n$ layers in the cloud of height $H$. Because the cross section of droplet is $\pi R^{2}$ the volume is $V=\pi R^{2}H$ and the mass of droplets in this volume is $m=n m_{0}=\frac{4}{3} \pi \rho_{0} n R^{3}$. The density of water in cloud is hence
$$\rho=\frac{m}{V}=\frac{4}{3} \frac{nR}{H} \rho_0$$
This parameter is experimentally measured and for average cloud (cumulus mediocris cloud) is has the value 1 $g/m^3$. Average cloud height is around 1000 $m$, average radius of droplet $15 \mu m$ and the density of water is $\rho_{0}=1000 kg/m^3$. Thus the indicative number of layers is $n = 12$. For this $n$ is the transmissivity 42\%.
For our case the transmissivity of clouds is 70\%, thus number of layers is $n = 8$.
\

We discovered that the cloud absorbs certain proportion of light irrespective of wavelength (in area of our interest 200-900 nm). In our case cloud can make very good correction of irradiance in our spectroscopic measurement.
\subsection{Determining errors}
\subsubsection{Measured variables}
\paragraph{Constants} Some of the measured variables are practically constant at the reached altitudes. They are gravitational acceleration, the spectroscopic variables and gas concentrations (except relative humidity). Here we calculate the arithmetic mean and the standard deviation of arithmetic mean. As some sensors output a near constant value (for example when they have a really long reaction time) the standard deviation would be quite small if not zero. Than we have to add an instrument error (we will add it to the standard deviation using Pythagorean addition). It is most significant in the gas sensors but as their datasheets don't provide the information and because it increases over time, we have to make an educated guess there. We multiply it by Student's coefficient for 99.9\% and the number of measurements of the specific variable. Therefore if any value that is measured on Earth or calculated from those data, the reference value should be within the deviation of the measured/calculated value. If it isn't we know with 99.9\% probability that there is a systematic error that caused it to deviate.
\paragraph{Variables linear with height} There is also a number of variables that change linearly with height. They are pressure, temperature and relative humidity. We calculate the slope and zero-intercept and the deviation. The deviation is equivalent to standard deviation for the constants, so we can do same operations with it.
\subsubsection{Calculated variables}
During calculations 
\subsection{Data measured}
As our CanSat stopped functioning just before launch, we are using data of the Irish team and our data measured on the ground where the Irish CanSat didn't contain the necessary sensors. The data measured on the ground is taken to be constant with altitude, which is likely for all the variables at the reached altitudes.
\subsection{Data obtainable from Earth}
\par These data about Kepler-62-f was measured by the Kepler probe based on the eclipse detection method. We also use this data in our models: \\\\
Radius - 1.41 radius of Earth\\
Mass - from 2.5 to 3 Earths\\
Semi-major axis - 0.718 AU\\
Circulation time - 267,291 earth days\\
Tilt slope - 89.90 degrees
\par
As we have these data for the target planet, we will use their equivalents for Earth while simulating the mission on Earth.
\subsection{Results}
\subsubsection{Variables linear with height}
\begin{figure}[!h]
\centering
\caption{Full range of measured temperature}

\label{temp1}
\end{figure}
\paragraph{Temperature.} In figure \ref{temp1}, there is a problem that if stationary, sunlight causes the CanSat to heat up. When it moves this effect is still present but hopefully negligable. To have more accurate result, we have to remove those data-points that deviate too much. From that we get figure \ref{temp2}.
\begin{figure}[!h]
\centering
\caption{Non-deviating data-points of measured temperature}

\label{temp2}
\end{figure}
\paragraph{Pressure.} The pressure measurements before launch were significantly deviated so they were removed from the data set. Even though pressure doesn't have a linear relationship (their real relationship is quazipolynomial close to an exponential converging to 0) the altitude difference during flight is low enough for linear relationship to be a close enough approximation, the result is shown in figure \ref{press}.
\begin{figure}[!h]
\centering
\caption{Non-deviating data-points of measured pressure}

\label{press}
\end{figure}
\paragraph{Humidity.} As relative humidity heavily depends on temperature it is better to plot absolute humidity. The problem is that the air in the cavity of the humidity sensor can have a slightly different temperature than the one in the temperature sensor. Even if they are a part of the same chip the air might not be as heated by the sun as the chip is. This causes the upward drift by both ends of figure \ref{hum1}. These values are removed in figure \ref{hum2}. That should provide a much more accurate measurement.
\begin{figure}[!h]
\centering
\caption{All data-points of absolute humidity}

\label{hum1}
\end{figure}
\begin{figure}[!h]
\centering
\caption{Non-deviating data-points of absolute humidity}

\label{hum2}
\end{figure}
\subsubsection{Numeric results before atmospheric analysis}
Some are directly measured, some are calculated, some are sea-level values for linear variables, with earth reference values in the right column where reasonable, $latm$ is local atmospheric pressure, therefore partial pressure in $latm$ is equivalent to the portion of mass of that compound in comparison to the mass of air:\\
\begin{align}
p_0 &= (1078\rpm10)hPa & p_0 &= 1013.25hPa \cite{pressx}\\
T_0 &= (24.1\rpm2.1)\degree C & T_0 &= 22.7\degree C \cite{tempx}\\
\Delta T_{100m} &= (0.8\rpm0.1)\degree C & \Delta T_{100m} &= 0.66\degree C\\
AH &= (1.237\rpm0.024)\% latm & & \\
g &= (9.31\rpm0.66)ms^{-2} & g_{ref} &= 9.81ms^{-2}\\
\rho_{air} &= (2.09\rpm0.14)kgm^{-3} & \rho_{ref} &= 1.23kgm^{-3}\\
\Phi_B &= (38.8\rpm5.4)\mu T & \rho_{ref} &= 44.0\mu T\\
h_{atmosphere} &= (133 \rpm 10) km & &\\
p_{O_2} &= (20\rpm2) \% latm & p_{O_2ref} &= 20.89 \% latm \cite{lastx}\\
p_{CO_2} &= (0.6\rpm0.1) \% latm & p_{CO_2ref} &= 0.5 \% latm\\
p_{O_3} &= (35\rpm 5) ppb & & \\
T_{ground\_average} &= (17\rpm5)\degree C &  T_{ground_ref}\ &= 15 \degree C \cite{Jacob}\\
Em_{2} &= (5.9\rpm1.5) MJ & & \\
f &= (0.81\rpm0.05) & f_{ref} &= 0,77\cite{Jacob}
\end{align}
We can see that magnetic field is bigger than necessary.
\subsubsection{Atmospheric gas concentrations}
After fitting concentrations of gases and the amount of clouds\footnote{Cross sections for calculated gases were taken from \cite{cross1}, \cite{cross2}, \cite{cross3}, \cite{cross4}}, we obtain a fit seen in figure \ref{spectrome}. As the precision of the measurements isn't very high some gas concentrations could be significantly different. The biggest problem is that some gasses are invisible at all frequencies (of those only noble gases with the exception of Argon are stable in an oxygen rich environment). Another group of gasses that cause Rayleigh scattering ($O_2$, $N_2$, $Ar$) and $NO_2$ which has an absorption curve very similar to Rayleigh scattering curve. $NO_2$, $NO$, $O_2$ and $NO$ have equilibrium reactions induced by sunlight \cite{no2o3}, because ozone and oxygen concentration measured are both lower than average value on Earth and $NO$ isn't a stable molecule, $NO_2$ must also have a lower concentration than on Earth. Therefore effects of $NO_2$ are negligible. With that in mind the only possible fit would imply more than half of the atmosphere being made up of Xenon or even more of Argon. We are disregarding all unstable molecules that are not made by natural processes (e.g. volatile organic chemicals). Such high concentration of noble gasses is extremely unlikely in so high quantities as was explained in \ref{basic}, paragraph Atmospheric composition.\par
\begin{figure}[!h]
\centering
\caption{}

\label{spectrome}
\end{figure}
So we conclude that air density measurement is wrong and will only calculate with overall atmosphere mass, not the density. From this we get concentrations of gasses that affect the incoming radiation, reference values on the right:\\
\begin{align}
p_{N_2} &= (79\rpm10) \% latm & p_{N_2ref} &= 78.08 \% latm \cite{lastx}\\
p_{H_2O} &= (0.4\rpm0.2) \% latm & p_{O_2ref} &= 28.08 \% latm\\
p_{O_3} &= (1.4\rpm0.2) 10^{-4} \% latm & p_{O_2ref} &= 0.5 10^{-4} \% latm
\end{align}
We cannot be sure whether part of the nitrogen isn't Argon because they behave the same way spectrocopically and have nearly the same molecule mass. Ozone and water concentrations change a lot with height so it is correct that the value is different form the one at ground level. This is an average over the whole atmosphere. There is also a cloud cover or a large amount of particles in the air (aerosol or dust). How the result is influencing the light received on earth is in figure \ref{spectrocal}, partial effects on it in Appendix 1.
\begin{figure}[!h]
\centering
\caption{Recieved power at different wavelengths outside atmosphere, on a sunny day and on a slightly cloudy day as was when we measured}

\label{spectrocal}
\end{figure}
\paragraph{Greenhouse effect.} When we apply the greenhouse calculations on these results into greenhouse effect calculations, we get that no other greenhouse gasses are necessary for the desired effect. Because water level in the air is influenced by temperature, figure \ref{gr2} doesn't contain it and contains only the driving greenhouse gasses.
\begin{figure}[!h]
\centering
\caption{All greenhouse gasses}
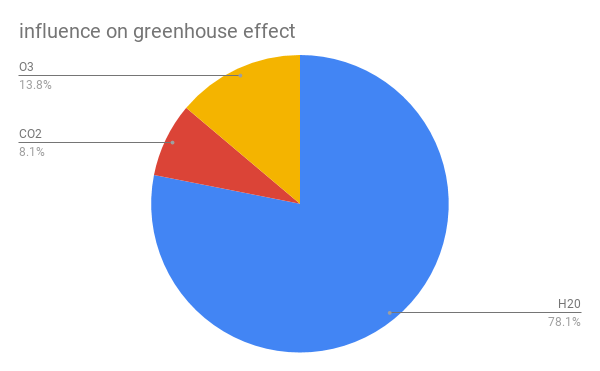
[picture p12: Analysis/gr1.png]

\label{gr1}
\end{figure}
\begin{figure}[!h]
\centering
\caption{Driving greenhouse gasses}
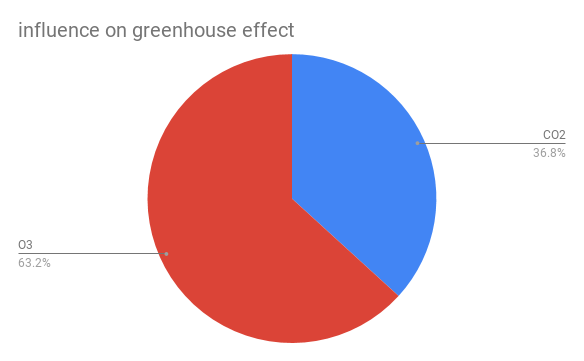
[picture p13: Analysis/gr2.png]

\label{gr2}
\end{figure}
\section{Biological experiments}
\subsection{Methods}
\par
The CanSat had an sticky flycatcher attached to its side. An excavator took a sample of soil after landing. After the satellite was recovered, it was locked into an airtight metal box. It was opened in an airtight chamber which we constructed.
\par
The chamber for the biological experiments is airtight yet openable. During the first use and after each opening, it is sufficient to have samples isolated in a metal box and to irradiate the chamber for a few minutes with an internal UVC fluorescent lamp. \cite{Allen}
\begin{figure}[!h]
\centering
\caption{UVC mutation mechanism taken from \cite{Allen}}
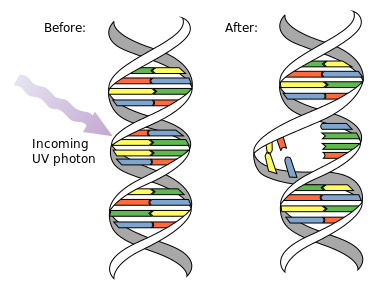
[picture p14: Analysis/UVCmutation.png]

\end{figure}
The radiation of wavelength of 253.7 nm destroys the nuclei of the cells of all living organisms. UV light of a lower wavelength than 345 nm does not pass through the acrylic, so it is ideal to use acrylic for the shielding as well as it is transparent. \cite{Eplastics} At the same time, the UVC lamp generates lethal ozone, which is then removed by freon. 
\begin{align}
O_2 &\xrightarrow{\text{UVC}} O + O \\
O_2 + O &\xrightarrow{\text{UVC}} O_3
\end{align}
\par
We used Freon named "22", which is actually chlorodifluoromethane ($CHClF_2$). Ozone degradation works by a series of reactions. We assume that there were the following reactions between Freon 22 and ozone:\\
\begin{align}
Cl + O_3 &\xrightarrow{} ClO + O_2 \\
ClO + O &\xrightarrow{} Cl + O_2
\end{align}
\par And
\begin{equation}
O_3 + 2_H^+ + 2e^- \xrightarrow{} O_2 + H_2O
\end{equation}
\par After decontaminating and neutralising whole chamber and all equipment inside, it is possible to remove the samples from the box and work with them. The chamber also includes a heater, a water dispenser, a lighting and a fan. Using these devices, ideal cultivation conditions can be achieved, which boosts the growth of the bacteria. The normal cultivation time is 48 hours, which we did not have in the finals, but with the help of all the upgrades we managed to grow some samples. Sample identification was achieved with the help of an integrated microscope with internal motion. This invention allowed us to still plug the eyepiece into the wall, but it lead to the oscillation of the setup, thus worsening the observation conditions. All interior equipment was handled through wall-mounted gloves.
\begin{figure}[!h]
\centering
\caption{UVC radiation source on}

\end{figure}
\par
Outside the chamber, three agar samples were mixed. We cleaned them with UVC and ozone with the rest of the chamber. Then, within the chamber, we selected samples from the satellite. There were pieces of soil, a blade of grass. Also, small bugs came out of the satellite, another proof of life on the planet. Then, we applied antibiotics (Amoxicilin) to one of the samples. During the night the samples grew and we regularly observed them with the microscope. Since the start of an agar preparation phase, a camera has taken a photo every 10 seconds to avoid the manipulation with the samples.\footnote{The date and time were set incorrectly, but the chronological record ran correctly.}
\begin{figure}[!h]
\centering
\caption{Preparation of the agar}

\end{figure}
\par The basic analysis of the sample was the Gram method; one of the basic procedures in microbiology. Gram staining identified the bacteria as either Gram positive (G+) and Gram negative (G-). This division is based on a different structure of the bacterial wall. The samples were taken from the chamber around 6:30 local time. It left us only 2.5 hours until the final presentation. In such a short time it was not possible to visibly grow colonies that would not come from the original sample.
\begin{enumerate}
  \item The selected sample was transferred to the slide. This sample was put into the flame of the candle for a few seconds. The sample temperature could not exceed 80 degrees Celsius.
  \item Crystal violet was applied to the preparation for two minutes.
  \item Subsequently, it was necessary to turn violet and apply Gram's reagent to the sample, which is an aqueous solution of potassium iodide and crystalline iodine at a concentration of 2 to 1. Then, we waited until the whole sample turned black.
  \item We washed the sample with 96\% ethanol until the reagent flowed out of the sample.
  \item We carefully rinse the sample with water for about two minutes.
  \item The last staining was done with safranin, lasting for as long as five minutes.
  \item Again, we washed the dye with water. Then, we dried the sample. Gram method was finished.
\end{enumerate}
\begin{figure}[!h]
\centering
\caption{Gram staining taken from \cite{Labfo}}
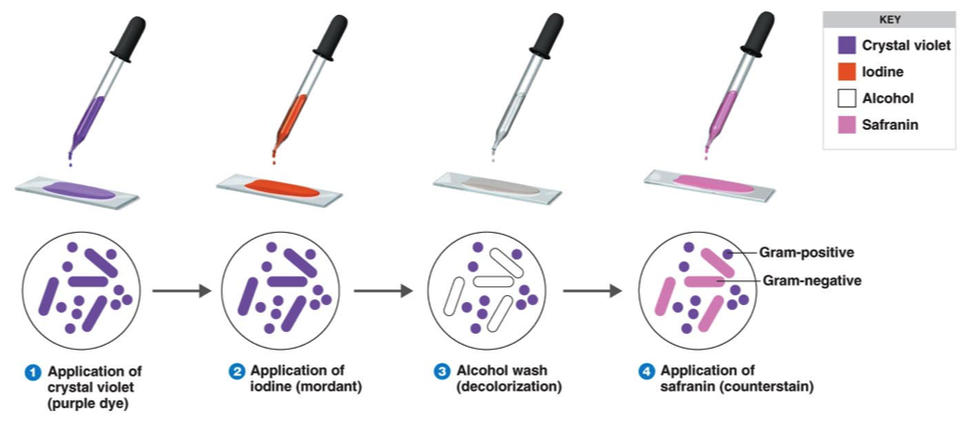
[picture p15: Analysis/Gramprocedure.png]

\end{figure}
\subsection{Results}
\par
Based on our experience from previous microscopy tests, we were able tu identify the group of Actinomycete belonging to gram-positive bacteria in the sample. Conversely, no gram-negative bacteria were identified. These results are in line with our assumptions. Gram-positive bacteria show the existence of life on the surface. On the other hand, negative analysis of gram-negative bacteria is also expectable. Gram-negative bacteria usually belong to dangerous pathogens, which are not to be expected in soil or air. Their presence would point to external contamination, which did not happen.
\par
As was mentioned in part above, several beetles and a blade of grass were trapped by the sticky insect trap. Therefore, it is possible to consider a very diverse life on the surface of the planet under investigation.
\par
In total, we created four samples. First of them was the specimen where we covered the surface of the agar with antibiotics. Gram method did not show any signs of life, so it did not differ from the reference. Based on our observation we can assume that the antibiotics functioned correctly and this experiment was set up correctly. Sample number two included small, partially scattered colonies of Gram-positive bacteria, which corresponds to the fact that these colonies originate from atomised clay that was obtained from our Cansat.
\begin{figure}[!h]
\centering
\caption{Sample number two}
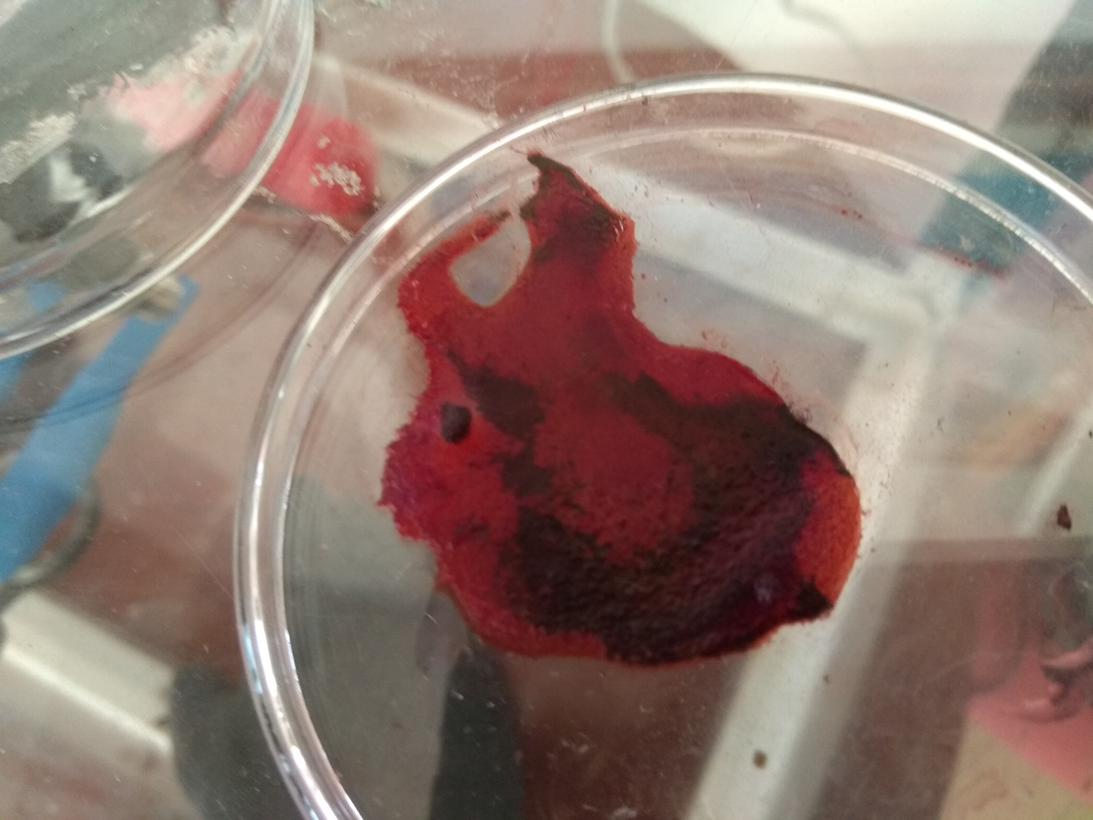
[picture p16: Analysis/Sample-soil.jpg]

\end{figure}
\par
Sample number three shows a distinct colony of Gram-positive bacteria. The reason is that the sample contained a blade of grass containing various bacteria whose colonies grew around the stem.
\begin{figure}[!h]
\centering
\caption{Sample number three}
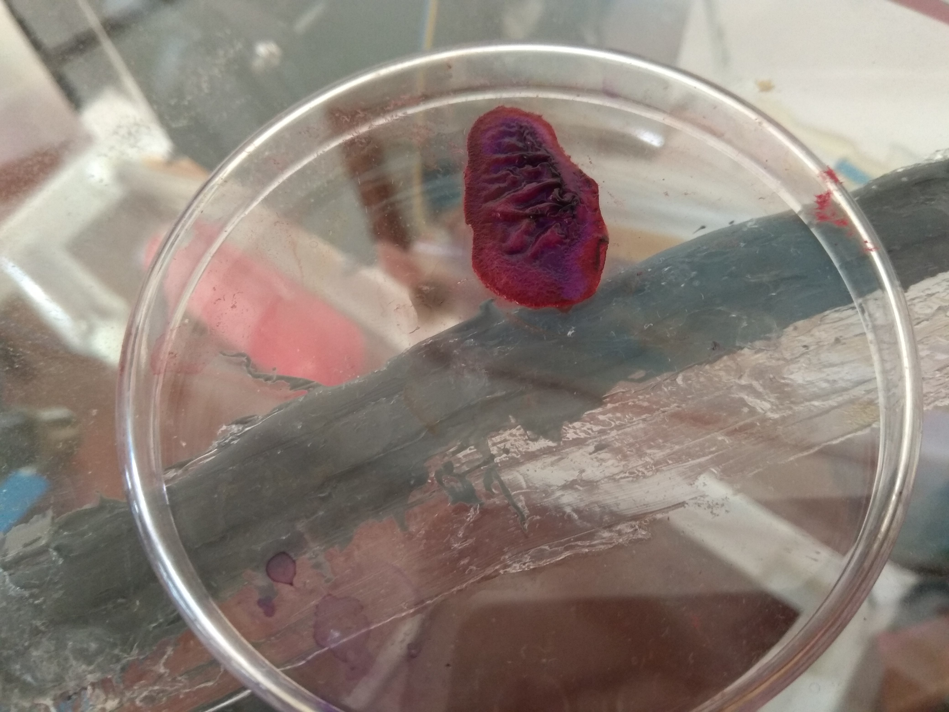
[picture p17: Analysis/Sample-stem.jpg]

\end{figure}
\par
The last sample fully met our expectations because Gram staining was negative - in other words, there were neither Gram-positive nor Gram-negative bacteria. This sample was clear and should confirm that no samples were contaminated in the chamber or during staining.
\begin{figure}[!h]
\centering
\caption{Reference sample}
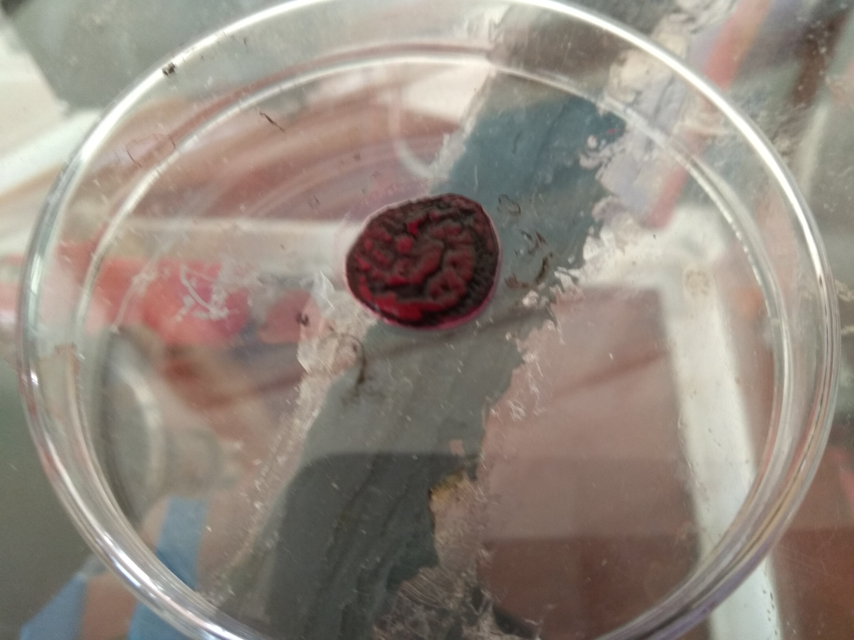
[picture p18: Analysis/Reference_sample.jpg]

\end{figure}
\section{Discussion}
\subsection{Biological experiments}
\par
Referring to the results (especially to the negative reference sample), it can be argued that our method of chamber cleaning and sample isolation was conclusive. Gram-negative or Gram-positive bacteria could not be introduced. It should be noted that there is also a group of gram-neutral bacteria that do not interact with a given colouring method. Their occurrence was not detected, but it was not even announced. It is most likely that our samples handling is fully valid.
\subsection{Basic variables}
The biggest problem is with the slope in pressure measurements. It should be much smaller and it propagates into unusual air density. It is possible that it was caused by a leak of some unusual gasses (for example Xenon as suggested in results or some heavy organic gas) but that is quite unlikely but if it were true (if supported by other measurements) it would signify either volcanic or industrial activity. Another possibility is a drift (a change over time) either induced by climate or by sensor fault but the change stops when the CanSat reaches ground so that is ruled out. Last possibility is sensor fault. Other variables came within error margin of the reference value so that is ok.
\subsection{Spectroscopic measurements}
The level of precision of the measurements was quite low so it is impossible to take the results as certain. They are however the most likely results with the level of detail our model simulates. There is propably a relation with amount of UV from the star and overall ozone levels, but neither of us is a chemist so we didn't calculate such longtime equilibrium. The major problems with spectroscopy are exchangeable gases. We calculated corectly the sum of nitrogen and argon but their respective values.
\subsection{Greenhouse effect calculations}
This is an approximation of very complex phenomena. Not all of them have been explored yet, so the functionality of the model is limited to the troposphere. Then, all radiation from Earths surface is considered to be long-wave. Also the errors from spectroscopic analysis propagated here. This was especially the case fore ozone for which $7/4$ of standard value were calculated. This is possible on Earth but it happens extremely rarely. That caused ozone to be majority greenhouse gas even though it usually accounts for about one third. That in turn caused no need for other gasses, which on Earth exist.
\section{Conclusion}
We successfully proved all the necessary conditions for life to exist we could think of. The atmosphere is most likely nice and everything else is with near certainty. The only thing we didn't test directly was radioactivity but the life we found would unlikely have been there if there was an unreasonable amount of it. We found microscopic life - some bacteria - and macroscopic life - a plant and a bug. This is a final proof of habitability.
\begin{acknowledgements}
The project has also been assisted our teacher Mgr. Lenka Vinklerová, post-analysis has been assisted by Š. Karch,
\end{acknowledgements}
%-------------------------------------------------------------------

\begin{thebibliography}{}

%  \bibitem{baker} EXAMPLE: Baker, N. 1966,
%      in Stellar Evolution,
%      ed.\ R. F. Stein,\& A. G. W. Cameron
%      (Plenum, New York) 333

  \bibitem{Allen} \href{https://earthobservatory.nasa.gov/Features/UVB/}{NASA EO/Jeannie Allen - 	
Ultraviolet Radiation: How it Affects Life on Earth}

  \bibitem{Giesen} \href{http://www.jgiesen.de/astro/solarday.htm}{Giesen Juergen - How to compute the length of a day}
  
    \bibitem{Strobel}\href{http://www.astronomynotes.com/solarsys/s3c.htm} {Nick Strobel, Astronomynotes - Surface temperature}
    
    \bibitem{Geocraft}\href{http://www.geocraft.com/WVFossils/greenhouse_data.html} {Geocraft - Water Vapor Rules the Greenhouse System}

    \bibitem{TBZ}\href{https://stavba.tzb-info.cz/docu/tabulky/0000/000086_katalog.html}{TZB - Material properties catalogue}

    \bibitem{Jacob}\href{http://acmg.seas.harvard.edu/people/faculty/djj/book/bookchap7.html}{Daniel Jacob - Chapter 7 The Greenhouse Effect in Introduction to Atmospheric Chemistry}

\bibitem{Labfo}\href{https://laboratoryinfo.com/gram-staining-principle-procedure-interpretation-and-animation/} {LaboratoryInfo - Gram Staining : Principle, Procedure, Interpretation and Animation}

\bibitem{Eplastics}\href{http://www.eplastics.com/plexiglass_acrylic_sheet_uv_filter} {Eplastics - Plexiglass Acrylic Sheet - UV Filtering}

\bibitem{cross1} \href{http://www.wmo.int/pages/prog/arep/gaw/documents/FINAL\_GAW\_218.pdf}{WMO}
\bibitem{cross2} http://irina.eas.gatech.edu/EAS8803\_Fall2009/Lec6.pdf {Georgia Institute of Technology - Irina Sokolik}
\bibitem{cross3} \href{https://www.colorado.edu/chemistry/volkamer/publications/group-pubs/thalman-2014-rscsNArO2air-accepted.pdf}{Colorado University}
\bibitem{cross4} Orphal, J. "A critical review of the absorption cross-sections of O3 and NO2 in the ultraviolet and visible." Journal of Photochemistry and Photobiology A: Chemistry 157.2-3 (2003): 185-209.

\bibitem{Humidity} Lawrence, Mark G. "The relationship between relative humidity and the dewpoint temperature in moist air: A simple conversion and applications." Bulletin of the American Meteorological Society 86.2 (2005): 225-234.

\bibitem{no2o3} https://earthobservatory.nasa.gov/Features/ChemistrySunlight/chemistry\_sunlight3.php

\bibitem{Trenberth} Trenberth, K. E., and C. J. Guillemot, 1994: The total mass of the atmosphere. J. Geophys. Res., 99, 23079–23088.

\bibitem{Tinetti} Tinetti, G \& Encrenaz, Thérèse \& Coustenis, Athena. (2013). Spectroscopy of planetary atmospheres in our Galaxy. The Astronomy and Astrophysics Review. 21. 10.1007/s00159-013-0063-6. 

\bibitem{Fritz} Fritz, Sigmund, (1949). THE ALBEDO OF THE PLANET EARTH AND OF CLOUDS. Journal of Meteorology, 10.1175/1520-0469(1949)006<0277:TAOTPE>2.0.CO;2  

\bibitem{Bhattacharyya} Bhattacharyya, Tapas, (2015). The Soil: A Natural Resource. ISBN: 81-903797-7-1

\bibitem {Ozone co2e} Life Cycle Assessment Methodology Sufficient to Support Public Declarations and Claims, Committee Draft Standard, Version 2.1. Scientific Certification Systems, February 2011. Annex B, Section 4. %( Wiki - Ozone "48")
\bibitem {Git-Circuit}\href{github.com/suchanekj/CanSatGOSA/tree/master/CanSat2.0/Schematics/Circuit}{Github/../Circuit}

\bibitem {Git-Code}\href{https://github.com/suchanekj/CanSatGOSA/tree/master/CanSat2.0/Code} {Github/../Code}

\bibitem {Websites} \href{gosa.cz}{gosa.cz}

\bibitem{droplet radius} \href{https://www.atmos-chem-phys.net/7/3507/2007/acp-7-3507-2007.pdf}{atmos-chem-phys}

\bibitem{density of cloud} \href{https://water.usgs.gov/edu/watercycleatmosphere.html}{USGS}

\bibitem{refra} Sæmundsson, Þorsteinn (1986). "Astronomical Refraction". Sky and Telescope. 72

\bibitem{tempx} Joao Paulo Ii, Portugal History | Weather Underground. Weather Forecast & Reports - Long Range & Local | Weather Underground [online]. Copyright © Copyright TWC Product and Technology LLC 2014, 2018 [cit. 15 July 2018]. Website: https://www.wunderground.com/history/daily/LPPD/date/2018-6-26?req\_city=Ponta\%20Delgada&req\_statename=Portugal
\bibitem{pressx}International Civil Aviation Organization. Manual of the ICAO Standard Atmosphere, Doc 7488-CD, Third Edition, 1993. ISBN 92-9194-004-6.
\bibitem{lastx}Zimmer, Carl (3 October 2013). "Earth's Oxygen: A Mystery Easy to Take for Granted". New York Times. Retrieved 3 October 2013.

\end{thebibliography}
\newpage
\pagebreak
\clearpage
\section{Apendix 1}
\begin{figure}[!h]
\caption{Partial effects of different compounds of the atmosphere}

\end{figure}
\newpage
\pagebreak
\clearpage
\section{Apendix 2}
\begin{figure}[!h]
\caption{Sensitivity curves of different sensors}

\end{figure}

\end{document}

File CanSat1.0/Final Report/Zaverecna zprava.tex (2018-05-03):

\documentclass[a4paper]{report}
\usepackage[utf8]{inputenc}
\usepackage{chngcntr}
\usepackage[margin=1in,includeheadfoot,headheight=13.6pt,footskip=2cm]{geometry}
\usepackage{tikz}
\usepackage{amsmath}
\usepackage{pgfplots}
\usepackage{listingsutf8}
\usepackage{graphicx}
\usepackage[main=czech]{babel}
\usepackage[utf8]{inputenc}
\usepackage{graphicx}
\usepackage{amsfonts}
\usepackage[colorlinks=true,urlcolor=blue]{hyperref}
\usepackage{eurosym}
\usepackage{chemfig}
\usepackage[version=4]{mhchem}
\usepackage{multicol}
\usepackage{titlesec}
\usepackage{float}
\usepackage{fancyhdr}
\usepackage{array}
\usepackage{longtable}
\usepackage{dirtytalk}
\pdfminorversion=5 
\pdfcompresslevel=9
\pdfobjcompresslevel=2
\newcolumntype{L}[1]{>{\raggedright\let\newline\\\arraybackslash\hspace{0pt}}m{#1}}
\newcolumntype{C}[1]{>{\centering\let\newline\\\arraybackslash\hspace{0pt}}m{#1}}
\newcolumntype{R}[1]{>{\raggedleft\let\newline\\\arraybackslash\hspace{0pt}}m{#1}}
\newcommand{\comm}[1]{}
\newenvironment{MulticolFigure}
  {\par\medskip\noindent\minipage{\linewidth}}
  {\endminipage\par\medskip}
\title{Závěrečná zpráva Hatalom}
\author{Patrik Novotný, Jakub Suchánek, Lukáš Vőlfl,\\Jan Janoušek, Jakub Zeman, Martin Vítek a vedoucí Mgr. Lenka Vinklerová}
\date{2018}
\counterwithout{section}{chapter}
\newcommand{\sectionbreak}{\clearpage}
\def\tick{\tikz\fill[scale=0.4](0,.35) -- (.25,0) -- (1,.7) -- (.25,.15) -- cycle;}
\pagestyle{fancy}
\fancyhf{}
\fancyhead[RO, LE]{\scshape\nouppercase{\leftmark}}
\fancyfoot[RO, LE]{\thepage}
%\fancyhf{}
\fancyhead[C]{Gymnazium Opatov Space Agency - Hatalom 2018}
\fancyfoot[R]{}
\fancyfoot[C]{\thepage}
\renewcommand{\headrulewidth}{0.7pt}
\renewcommand{\footrulewidth}{0.7pt}
\setlength{\parskip}{5pt}
\begin{document}
\begin{titlepage}
    \centering
    \vfil
    
    \vfill
    {\bfseries\Large
        Závěrečná zpráva\\
        Hatalom\\
        2018\\
    }
    \vskip2cm
    \large Patrik Novotný, Jakub Suchánek, Lukáš Vőlfl, Jan Janoušek, Jakub Zeman, Martin Vítek\\
    \vfill
    \large Vedoucí Mgr. Lenka Vinklerová\\
    \vfill
    \vfill
\end{titlepage}
% Takto komentujte text.
\comm{nebo takto}
\tableofcontents
\section{Úvod}
\paragraph{} V rukou právě držíte závěrečnou práci shrnující fakta projektu CanSat Hatalom, který stavěli členové GOSA neboli Gymnazium Opatov Space Agency. V posledních šesti měsících jsme založili agenturu GOSA, která zaštítila na našem gymnáziu veškerý vědecký a technický vývoj, nejenom soutěž CanSat. Navázali jsme kontakty, získali peníze, naučili se řádně plánovat, konstruovat a třeba i vymýšlet testy částí projektu, což se ukázalo jako velmi důležité. Také jsme se naučili, jak si dělit práci. Rozhodli jsme se výsledky naší práce poskytnout všem, proto také je náš projekt opensourcovou záležitostí. Projekt byl náročný vzhledem k tomu, že jsme všichni maturanti, ale stál za to a dal nám mnoho. Přečtete-li si tedy další části zprávy, tak nejenže zjistíte, jak co funguje, ale i proč a jak jsme dané řešení zvolili.
\section{Náš tým}
\begin{multicols}{2}
\begin{center}
\begin{MulticolFigure}
\centering
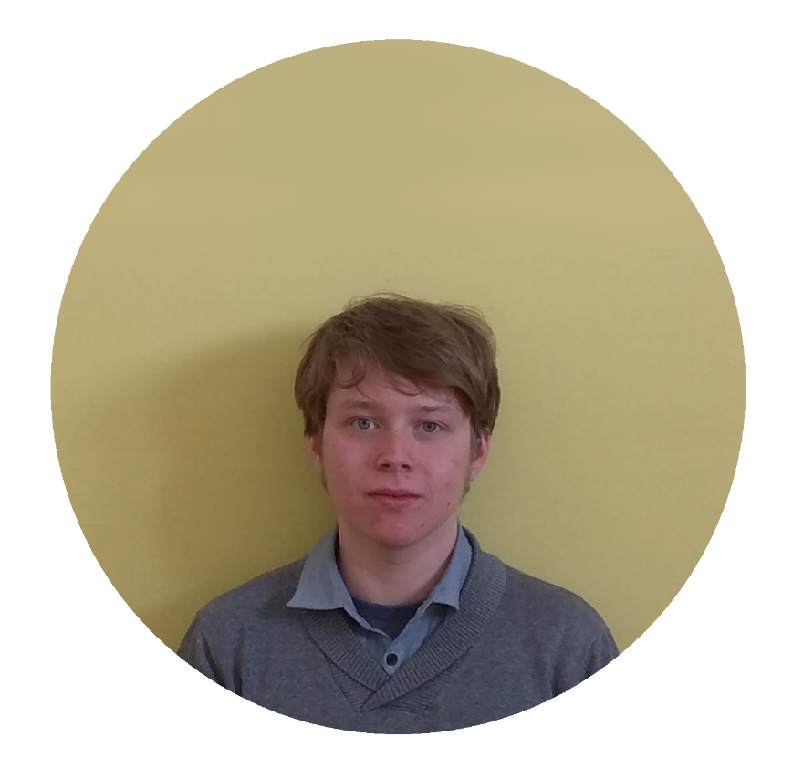
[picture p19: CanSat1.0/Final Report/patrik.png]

\end{MulticolFigure}
\paragraph{} \large Patrik Novotný – kapitán
\paragraph{} \normalsize Konstrukce desinfekční komory, právo, finance
\begin{MulticolFigure}
\centering
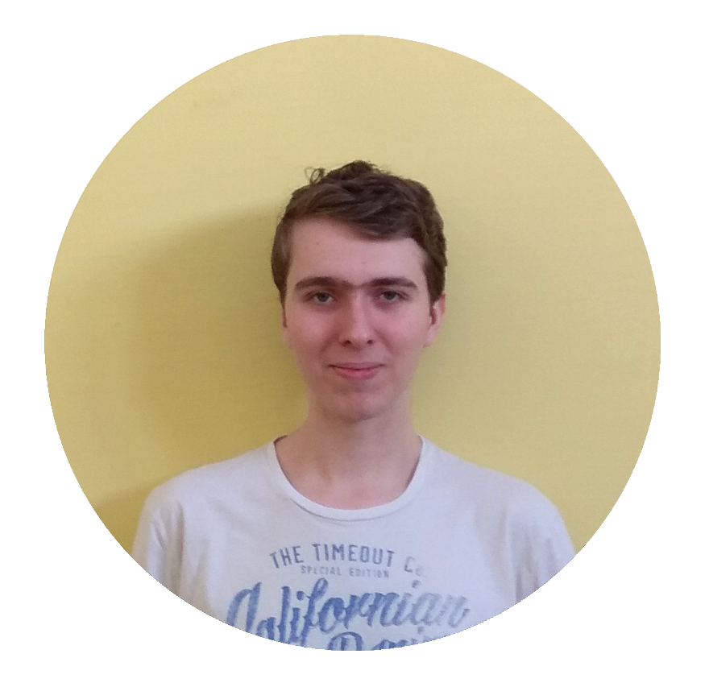
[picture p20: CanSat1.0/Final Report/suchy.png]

\end{MulticolFigure}
\paragraph{} \large Jakub Suchánek – šéftechnik
\paragraph{} \normalsize Celkový design CanSatu, tvorba softwaru pro řídící obvod
\begin{MulticolFigure}
\centering
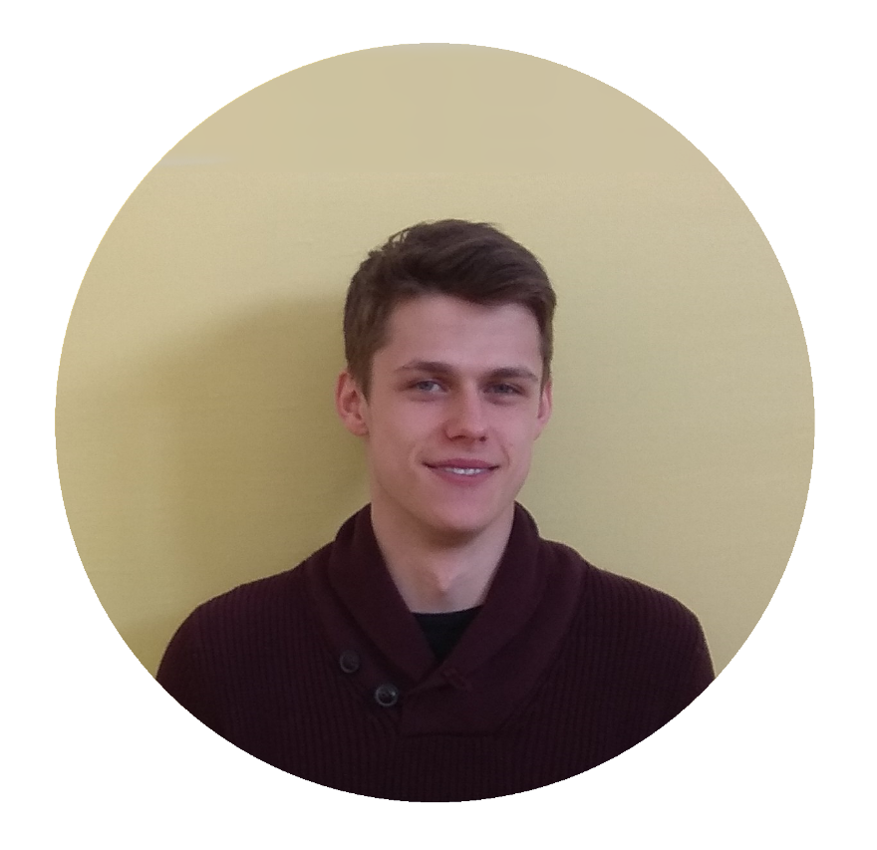
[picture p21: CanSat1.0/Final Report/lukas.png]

\end{MulticolFigure}
\paragraph{} \large Lukáš Vőlfl – konstruktér, dronař
\paragraph{} \normalsize Ovládání drona při testech, design letových subsystémů
\begin{MulticolFigure}
\centering
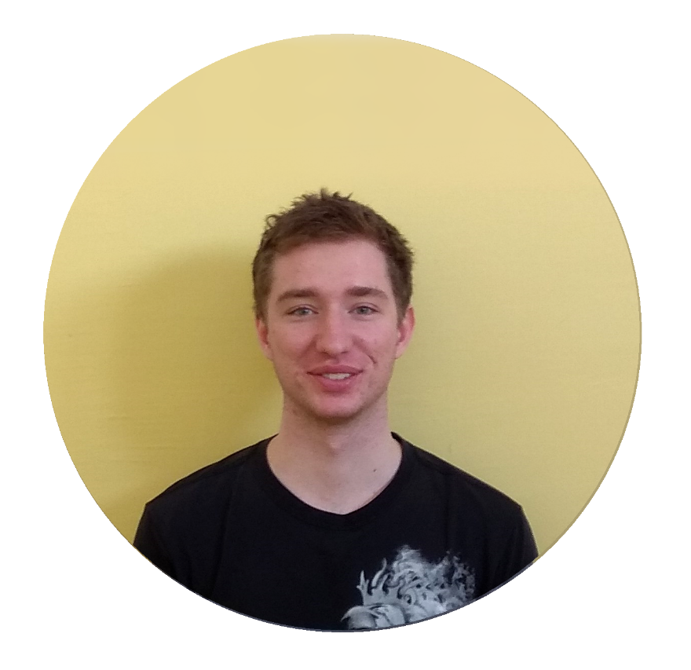
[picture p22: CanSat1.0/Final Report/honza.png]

\end{MulticolFigure}
\paragraph{} \large Jan Janoušek – PR a HR odborník
\paragraph{} \normalsize Propagace na sociálních sítích, komunikace se sponzory
\begin{MulticolFigure}
\centering
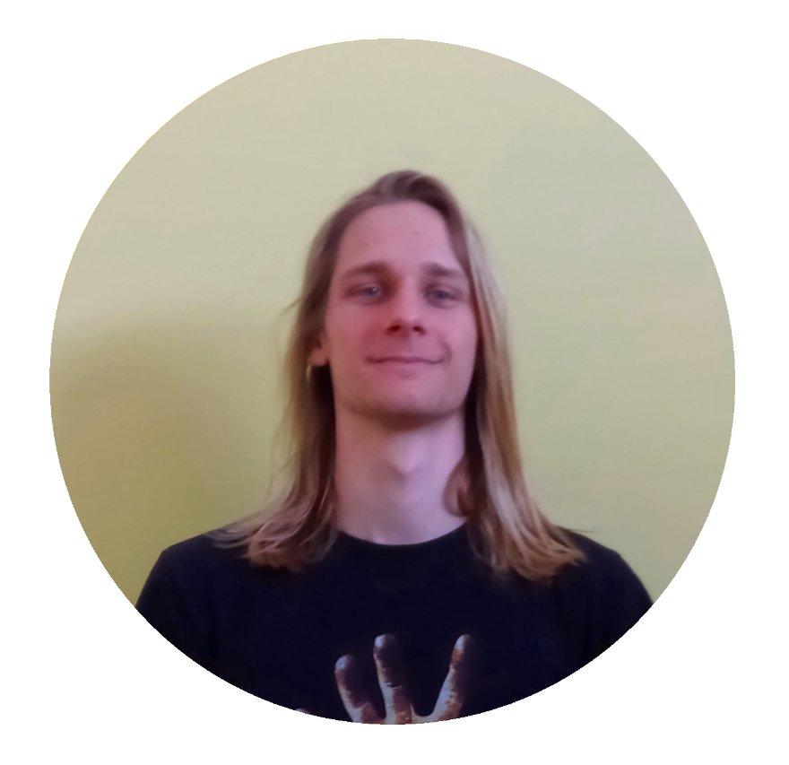
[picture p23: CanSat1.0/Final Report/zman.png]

\end{MulticolFigure}
\paragraph{} \large Jakub Zeman – konstruktér, bezpečnost práce
\paragraph{} \normalsize Pájení, sestavení a opravy CanSatu
\begin{MulticolFigure}
\centering
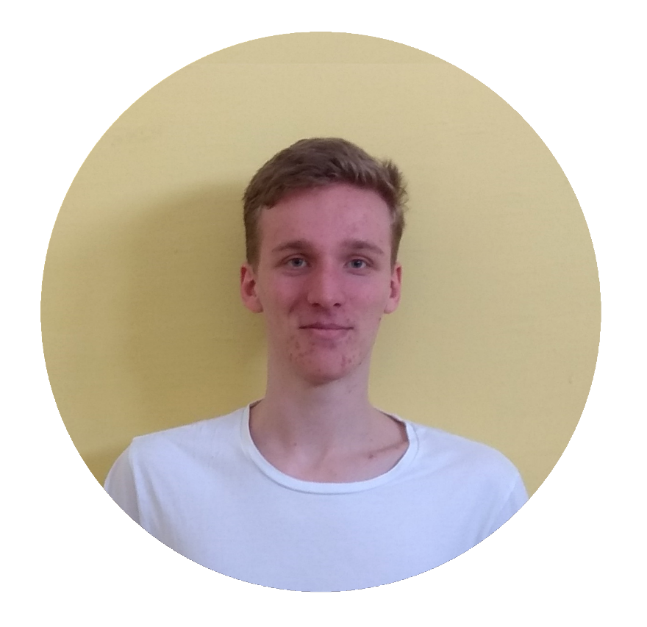
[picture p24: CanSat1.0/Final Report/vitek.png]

\end{MulticolFigure}
\paragraph{} \large Martin Vítek – programátor
\paragraph{} \normalsize Vývoj webu, finance
\end{center}
\end{multicols}
\paragraph{} Mimo svoje pozice se dělíme do týmů dle daného úkolu - hlavně programátorský (Jakub Suchánek, Patrik Novotný a Martin Vítek) a konstrukční (Jakub Zeman, Lukáš Vőlfl a Jakub Suchánek), Jan Janoušek obstarává provozní činnosti.
\subsection{Letové pozice}
\paragraph{} Speciálně pak máme vyčleněny pozice pro let (v současné době se prakticky týká pouze testů komponent). Pro neexistenci českých ekvivalentů užíváme anglických názvů:
\paragraph{} Mission Manager – Patrik Novotný
\paragraph{} Payload Manager – Jakub Suchánek
\paragraph{} Flight Director – Lukáš Vőlfl
\paragraph{} Safety Officer– Jakub Zeman
\section{Průběh prací}
\begin{itemize}
\item Říjen: Na začátku října jsme začali rozmýšlet, jakou si zvolíme sekundární misi. Měli jsme tři různé varianty řešení a to:
\begin{itemize}
\item Řiditelný padák
\item Letadlo
\item Dron/Helikoptéra
\end{itemize}
Každý si vybral, která z variant se mu líbí, a snažil se ji obhájit a zároveň oponovat volbám ostatních. Tímto postupem jsme dospěli k závěru, že nejvhodnější a nejzajímavější řešení bude dron.
\item Listopad: Po definitivním rozhodnutí, že náš CanSat bude fungovat na způsob dronu, jsme začali kreslit návrhy a hledat optimální řešení konstrukčních problémů, např. způsob vysouvání ramen s rotory. Zároveň Jakub Zeman (po dlouhém rozvažování, zda anténu koupit nebo postavit) za pomoci různých všedních i nevšedních nástrojů (lahev od kečupu) vyrobil anténu. Dne 9. listopadu jsme se sešli s Klubem přátel gymnázia Opatov (KPGO) a požádáli o sponzoring. Náš projekt se jim velice líbil a slíbili nám finanční podporu.
\item Prosinec: Jakub Suchánek začal rozkreslovat základní desku. Řešíme co všechno budeme chtít měřit a jaké senzory na CanSat dáme. V tomto rozhodování nám pomohla schůzka s Janem Horákem, který je členem týmu RAJsat, jenž v soutěži zvítězil v letech 2016 a 2017. Ukázal nám poslední verzi jejich satelitu, s nímž se zúčastnili evropského finále v roce 2017. I přesto, že jejich satelit se od naší vize výrazně lišil, odnesli jsme si ze setkání spoustu informací a inspirace. Honza nám dal spoustu rad vycházejících z jeho zkušeností, neboť nám i v následujících měsících poskytoval konzultace.
\item Leden: V lednu nás čekalo národní semifinále a tudíž byl nejvyšší čas testovat měření a přenos základních dat. Hned 4. ledna jsme se sešli za účelem otestovat spojení a kvalitu antény. Bohužel se vyskytla chyba, kterou se nepodařilo na místě opravit, takže jsme nedokázali vysílat ani na dva metry. Po prvním neúspěchu jsme se znovu sešli o týden později. Plán byl otestovat anténu na vzdálenost 1 km. Po úspěchu se skupinka s přijímací anténou rozhodla přesunout dále. Po dalším úspěchu jsme šli ještě dál. Nakonec jsme bez jakýchkoliv problémů jsme vysílali z Pankráce na Háje, což odpovídá vzdálenosti zhruba 6,5 km. Dále jsme nepokračovali, bylo to zbytečné a těžko by se hledalo místo, ze kterého by bylo možné přímé spojení.
\item Semifinále: 30. ledna nás čekalo republikové semifinále. Setkali jsme se v 8:30 na Opatově a přesunuli se před kancelář ESERO, kde jsme ještě trénovali prezentaci a ladili poslední detaily. První částí semifinále byl telemetrický test, kterého jsme se nijak nebáli, protože naše předchozí testy potvrdily kvalitu spojení. Druhou částí byla prezentace, ve které každý zmínil to hlavní, čím se zabýval, a společně jsme předložili naši vizi CanSatu s plány do budoucna. Porotě se náš nápad líbil, avšak  upozornila nás na jeho složitost a absenci příběhu, ten potom Patrik Novotný vytvořil a je k nalezení na našich webových stánkách a níže v této zprávě. Po odprezentování jsme odešli s pocitem dobře odvedené práce. Odpoledne byly zveřejněny výsledky a my jsme byli šťastni z třetího místa a z postupu do finále. Byla to odměna za naši dosavadní práci, ale i velký závazek do budoucna.
\item Únor: Po uspěšném postupu do národního finále, byl čas začít nakupovat potřebné díly. Zároveň jsme probírali možná řešení problémů jako sebrání vzorku půdy nebo přenos dat na web. V půlce února přišly součástky na pájení hlavního plošného spoje, a tak se Jakub Suchánek pustil do pájení, které bylo možné sledovat live na YouTube. Dne 22.února jsme se sešli u Lukáše Vőlfla za účelem testů stabilizačního padáčku a vypouštěcího zařízení. Porovnáním letu/pádu s padáčkem a bez něj jsme mohli brát testy za vydařené. Nejen, že padáček plechovku stabilizoval do správné polohy, ale i pád výrazně zpomalil. Honza Janoušek zajišťoval logistické úkoly.
\item Březen: Začátek března se nesl v duchu biologie. Patrik Novotný zkoušel, za jak dlouho vyroste na agaru kolonie bakterií z hlíny a pak i ze země. Také vyrobil UVtrubku (níže specifikována).  V půlce měsíce Jakub Zeman začal tisknout testovací CanSat hull, tudíž jsme se mohli připravovat na letové zkoušky. Dne 29. března jsme měsíc zakončili prvním testovacím letem Kosta Moisid, pojmenovaném po podporovateli. Během daného dne tým Jakub Zeman a Jakub Suchánek vyzvedl v Liberci finální a záložní verzi CanSatu. Součastně druhý tým v Praze testoval první let za pomocí motorů. Test dopadl úspěšně a potvrdilo se, že náš koncept je plně funkční a stačí ho do finále optimalizovat.
\item Duben: Měsíc jsme začali workshopem hned 1. dubna, kdy jsme testovali generátor \ce{O3}, zároveň jsme programovali a začali s přípravou průběhové zprávy. Celý duben do finále jsme testovali hardware i software a psali závěrečnou zprávu, v čemž nám pomáhaly konzultace s RajSat týmem. Největší událostí měsíce bylo jednání 9. dubna s KPGO, jelikož nás tento subjekt právně i finančně zajišťuje. Vysvětlili jsme průběh činností a výhledy do budoucna. KPGO schválilo, že při absenci další sponzorů, nám plně uhradí cestu na případné evropské kolo. Následně jsme si otevřeli ve škole stánek a prezentovali dosavadní vývoj projektu zletilým studentům, rodičům a podporovatelům naší školy. Zlatým hřebem měsíce pro nás bude CanSat národní finále na letišti Letkov a v Plzni 19. a 20. dubna. 
\end{itemize}
\section{Testy}
V průběhu projektu jsme podrobili jednotlivé součásti i celý CanSat sérii testů, ty nejdůležitější zde uvádíme.
\paragraph{} Testy padáčku proběhly během výběru variant, což bylo v průběhu listopadu. Ověřili jsme si stabilizační roli padáčku.
\paragraph{} Telekomunikační test 1 - bohužel neúspěšně jsme v průběhu ledna testovali přenos telemetrických dat.
\paragraph{} Telekomunikační test 2 - o týden později jsme provedli test znovu. Povedlo se nám přenášet data každou vteřinu na vzdálenost 6,5 kilometru v rozsahu směrování přijímací antény 20 stupňů.
\paragraph{} Crashtest a test padáku - v lednu jsme testovali výsledný padák a jeho schopnost otevřít ramena CanSatu a přibržďovat. Zde byl stále modelem rýžový CanSat, testy skončily crash testem, který nám sdělil, jak pevný musí být výsledný hull.
\paragraph{} UV testy probíhaly v březnu, kdy jsme nejprve testovali růst bakterií ze vzorku (hlína) i ze vzduchu a učili se poznat, jak daný organismus roste s časem. Následně jsme tyto organismy a květinu osení ozařovali UVC zářivkou.
\begin{figure}[H]
\caption{Biologické pokusy, zdroj: Patrik Novotný}
\centering
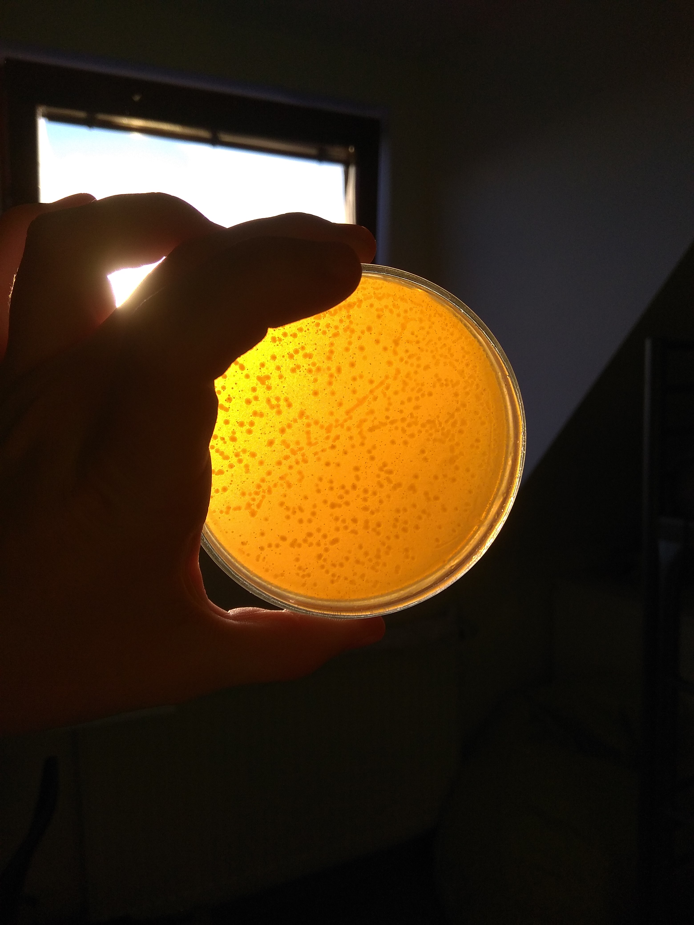
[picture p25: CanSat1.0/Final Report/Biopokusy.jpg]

\end{figure}
\paragraph{} Test Kosta Moisidis - První kompletní test, kde CanSat letěl v celku. Byl však pro jistotu ovládán dálkově. Test dopadl velmi úspěšně.
\paragraph{} Test Pepa Vu - Zde jsme testovali schopnost chytit CanSat do naší plachty o ploše 48 čtverečních metrů. Po počátečních nezdarech jsme se této nouzové činnosti naučili.
\paragraph{} Test všech systémů - finální test všech systémů nás čeká 15. dubna, kdy chceme testovat CanSat podmínkami tvrdšími, než čekáme.
\section{Příběh}
\paragraph{} Za každou událostí v dějinách stojí příběh, protože právě příběhy jsou tím, co člověka motivuje k činnosti. Jaký je náš příběh? Proč stavíme meziplanetární sondu? Simulujeme misi, ke které možná jednoho dne dojde. Cílem našeho zájmu je planeta obíhající kolem jiné hvězdy, která se jmenuje Kepler 62, okem byste ji neviděli. Je menší než Slunce. Z našich zemí se zdá, že nám obíhá vysoko nad hlavami v souhvězdí Lyry. Je od nás vzdálena skoro 1200 světelných let.
\begin{figure}[!h]
\centering
\caption{Soustava Kepler 62, zdroj:
\href{https://www.nasa.gov/mission_pages/kepler/multimedia/images/kepler-69-diagram.html}{NASA Ames/JPL-Caltech}}

\end{figure}
\paragraph{} Hvězd je ve vesmíru mnoho, astronomové by vám řekli, že v každé galaxii jich je přibližně \(10^{12}\) a tolik je i ve vesmíru galaxií. O to ale nejde. Je jich mnoho. A některé z nich mají i své planety. Kepler je právě takovou hvězdou, obíhá ho dle našich poznatků 5 planet, dvě obzvlášť zajímavé, označované jako „e“ a „f“. 
\paragraph{} Planeta „e“ leží na vnitřním okraji obyvatelné zóny. Jednoduše řečeno, předpokládáme-li podmínky pro vznik života, pak je moc teplá, má podobnou smůlu jako naše Venuše. Ovšem její sourozenec Kepler 62 f je nadějnější. Nemáme zdaleka všechna data, ale víme, že v dané oběžné vzdálenosti by planeta měla mít průměrnou povrchovou teplotu kolem -40 stupňů. Ovšem pokud by měla tlustší atmosféru (pětkrát) tvořenou \ce{CO2}, což není nic neobvyklého, pak by na většině povrchu planety mohla existovat voda v kapalném skupenství. Při tenčí atmosféře by se voda v kapalné fázi mohla vyskytovat jen v některých částech planety.
\paragraph{} Nyní ovšem k optimističtějším datům. Hvězda Kepler 62 je stabilní hvězdou (nízká hmotnost i metalicita vůči Slunci), navíc by měla zářit ještě dvakrát déle, než je stáří vesmíru. Planeta oběhne svou domovskou hvězdu za 267 dní, hvězda by ji tudíž neměla příliš negativně ovlivňovat. Celý systém je dle odhadů až o dvě miliardy let starší než náš. Naše cílová planeta má také pravděpodobně vlastní měsíc a skloněnou rotační osu, takže se na jejím povrchu mění roční období. Z těchto údajů lze odhadnout, že není lepší kandidát pro nalezení mimozemského života, byť lze předpokládat nižší stupeň vyspělosti vzhledem k tomu, že z planety nepřijímáme vysílání.
\paragraph{} Co a proč tedy hodláme na planetě uskutečnit?
\begin{itemize}
\item Z orbity získáme snímky planety – v našem případě Google Maps, dle snímků vybereme místo přistání.
\item Po průletu atmosférou rušící vysílání zahájíme samotnou misi – příjem signálu bude možný z výšky kolem 1-2 km nad povrchem, budeme udržovat rychlost klesání 6-12 m/s, abychom nepoškodili aparaturu v sondě ani nenarušili přenosy dat uskutečňované více způsoby.
\item Celou dobu letu budeme vysílat obraz. Je možné, že sice již nežije na planetě vyspělá civilizace, ale třeba žila a její pozůstatky budou viditelné.
\item Budeme měřit údaje nutné pro vznik života – množství \ce{CO2} a \ce{O2}, tlak a teplotu, a dále intenzitu magnetického pole
V poslední fázi mise odebereme malý vzorek horniny a zjistíme, zda nám v agaru nevyroste bakteriální život blízký pozemskému.
\end{itemize}
\paragraph{} Na reálnou misi na Kepler 62 f si budeme muset jistě nějakou dobu počkat, ač se dá očekávat, že to bude jeden z prvních lidských mezihvězdných cílů. Na simulaci mise však čekat nemusíme!
\section{Plánovaný průběh mise}
\subsection{Předletová příprava}
\paragraph{} Před startem CanSatu je nutno zkontrolovat a popř. dobít baterie CanSatu. Poté vyberou pořadatelé místo dopadu z mapy, to se zanese do Groundstation. Zapne se a zkalibruje jak GPS, tak flight controller, který musí být zapnut v rovnovážné poloze. Mezi tím bude v UV trubce ozařována mistička s agarem a rypadlo CanSatu. Při tomto ozařování vzniká \ce{O3}. Poté, co se UV trubka vypne, tak se do ní vloží pro větší dekontaminaci celý CanSat, v němž \ce{O3} zahubí další bakterie, avšak narozdíl od UV záření nepoškodí jeho vnitřní vybavení. Následně může CanSat Hatalom odstartovat. Tento způsob dekontaminace jsme otestovali na mikroorganismech i rostlinách, na zvířatech jsme tak z etických důvodů nečinili.
\subsection{Průběh letu}
\paragraph{} Po vypuštění satelitu se otevře malý padáček sloužící jak ke stabilizaci, tak k mírnému brždění. Vlivem uvolnění CanSatu dojde k otevření ramen a spuštění motorů. CanSat bude automaticky pomalu klesat k místu, které před startem zvolili pořadatelé jako místo přistání. Polohu si v průběhu letu CanSat kontroluje pomocí tlakoměru a GPS. Když se přiblíží k zemi na vzdálenost metrů, tak začne vyhodnocovat vhodné místo k přistání. Pomocí čidel vzdálenosti najde místo podobně vzdálené od všech čtyř čidel (bude se tedy jednat o rovinu) a pak přistane. Po přistání rýpne lopatka na servomotorku do země a následně do agaru, v něm po kontaktu s hlínou začne bujet život. Po celou dobu letu i po přistání bude CanSat odesílat údaje o teplotě, tlaku, poloze a množství \ce{CO2}.
\subsection{Vyhodnocení dat}
\paragraph{} Všechna naměřená data se budou posílat do Groundstation a odtud poputují na webové úložiště na našich stránkách. Už během letu se bude na webovkách objevovat poloha CanSatu v reálném čase. Ostatní data se budou zobrazovat na webu, ale vyhodnocovat a dávat do souvislostí se budou až po letu. Po vyjmutí misky s agarem ji Patrik Novotný nafotí a následně prozkoumá mikroskopem, analýzu zkoušel již doma. Stopy života je schopen analyzovat. S další analýzou (s co nejpřesnější identifikací - skupiny organismů či dokonce samotného druhu) mu pomůže po Skypu s námi spolupracující biologická konzultantka Barbora Haláková.
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

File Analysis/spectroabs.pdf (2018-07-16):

## Absorbtion and scattering of fitted gasses

argon scattering

g

e

t

s

t

nitrogen scattering

h

r

o

u

g

water vapour absorbtion; oxygen absorbtion

h []

ozone absorbtion; nitrogen dioxide absorbtion
oxygen scattering; overall

## wavelength [nm]

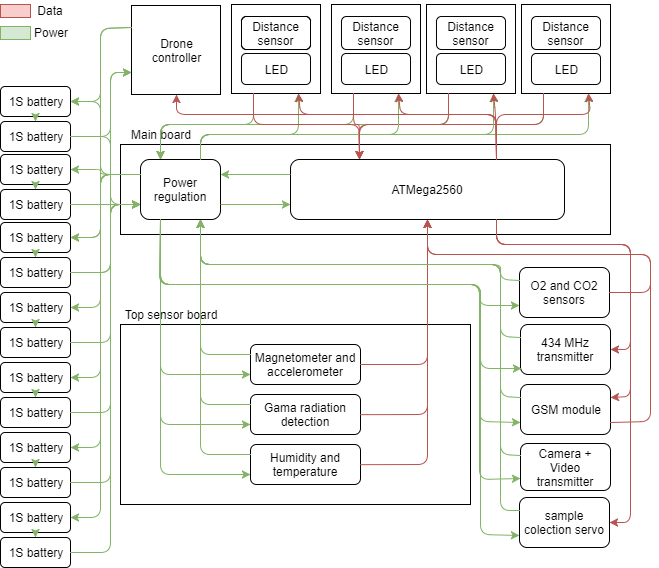
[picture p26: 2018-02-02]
CanSat1.0/Schematics/Circuit/CanSat.png

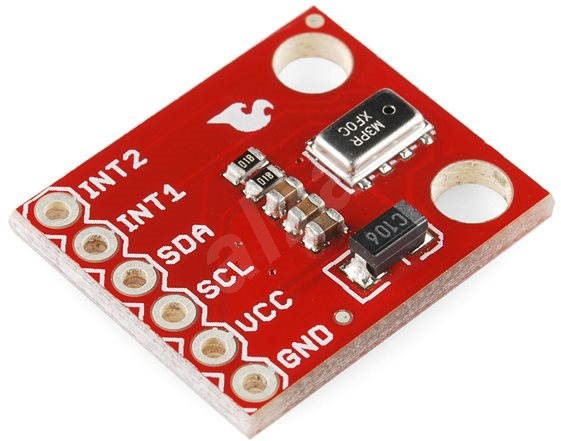
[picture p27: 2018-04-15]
CanSat1.0/Final Report/barometr.jpg

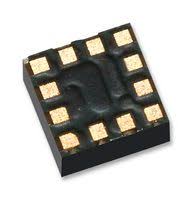
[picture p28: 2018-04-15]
CanSat1.0/Final Report/acc+mgn.jpg

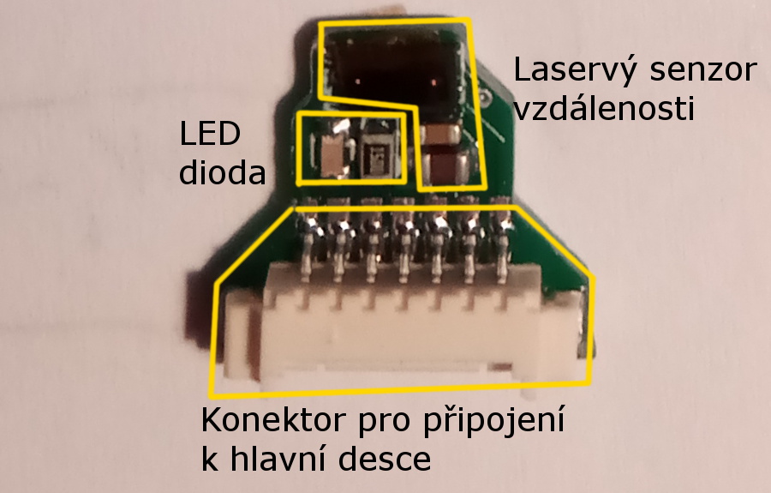
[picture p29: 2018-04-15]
CanSat1.0/Final Report/deska_rameno.jpg

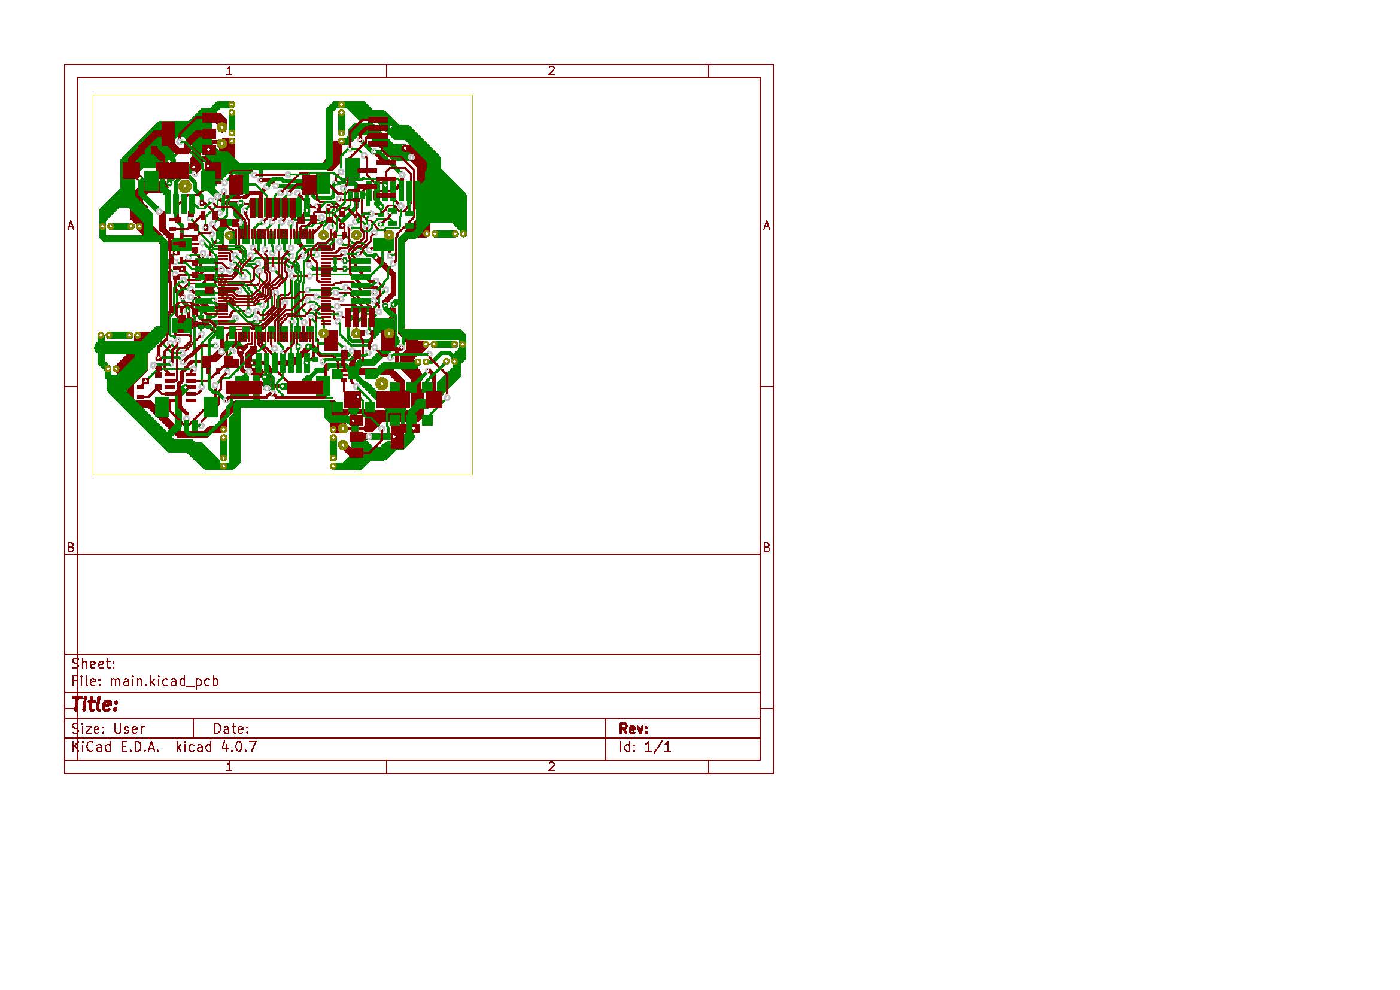
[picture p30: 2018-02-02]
CanSat1.0/Schematics/Circuit/main_pcb.jpg

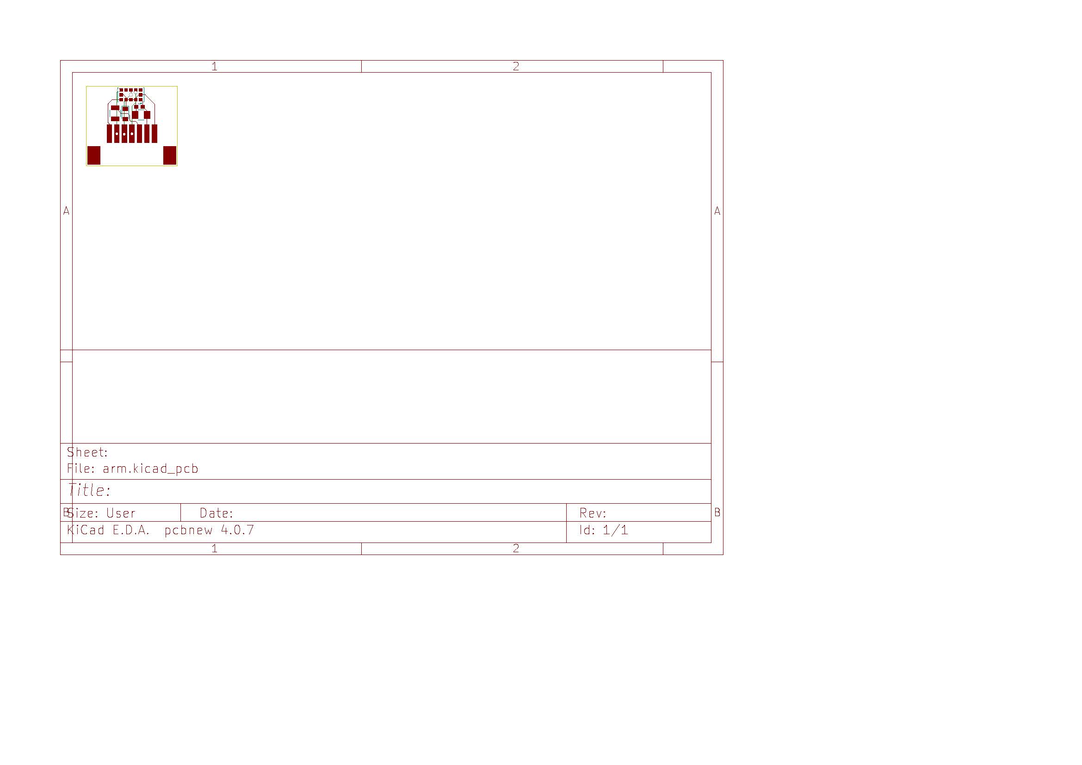
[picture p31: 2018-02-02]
CanSat1.0/Schematics/Circuit/arm_pcb.jpg

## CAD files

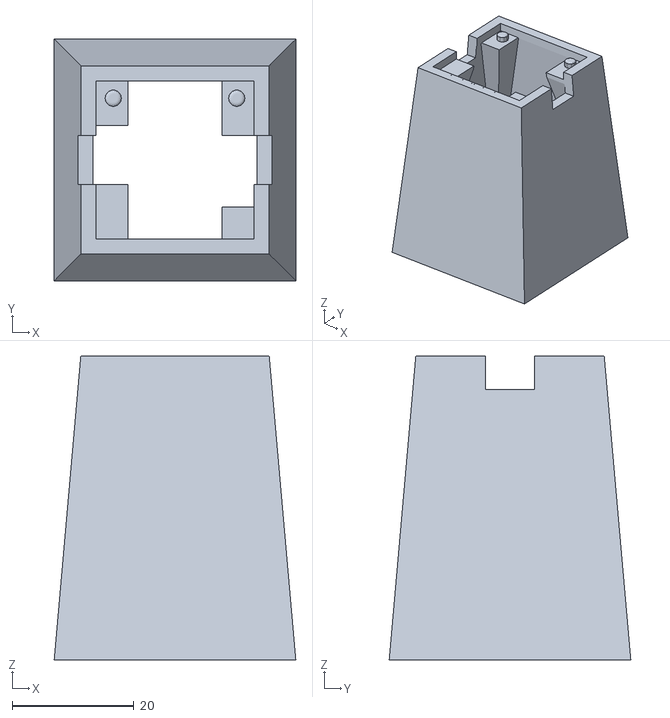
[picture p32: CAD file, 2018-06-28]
CanSat2.0/Code/CanSat_examples/Qwiic_Spectral_Sensor_AS726X-master/Qwiic_Spectral_Sensor_AS726X-master/Enclosure/AS726xBasicShroud.stl
39.7 x 39.7 x 50.0

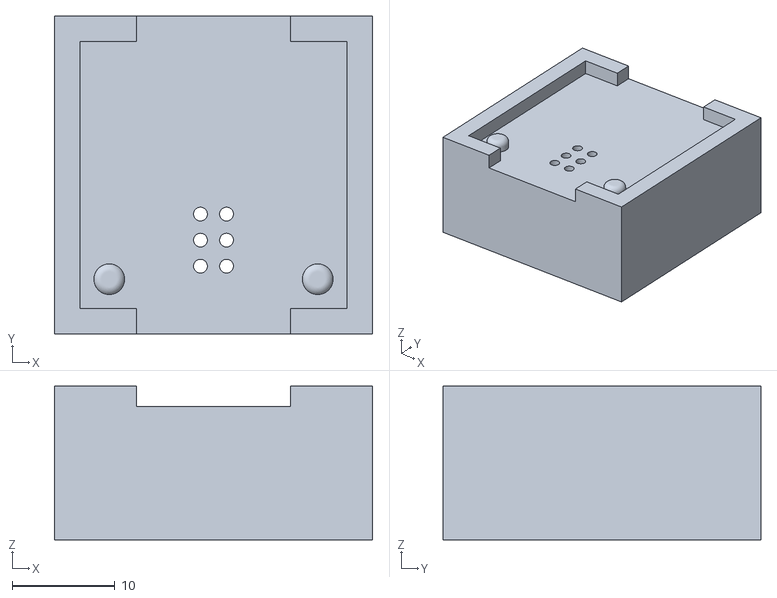
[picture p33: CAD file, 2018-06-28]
CanSat2.0/Code/CanSat_examples/Qwiic_Spectral_Sensor_AS726X-master/Qwiic_Spectral_Sensor_AS726X-master/Enclosure/Programmer/AS726xProgrammerLid.stl
31.0 x 31.0 x 15.0

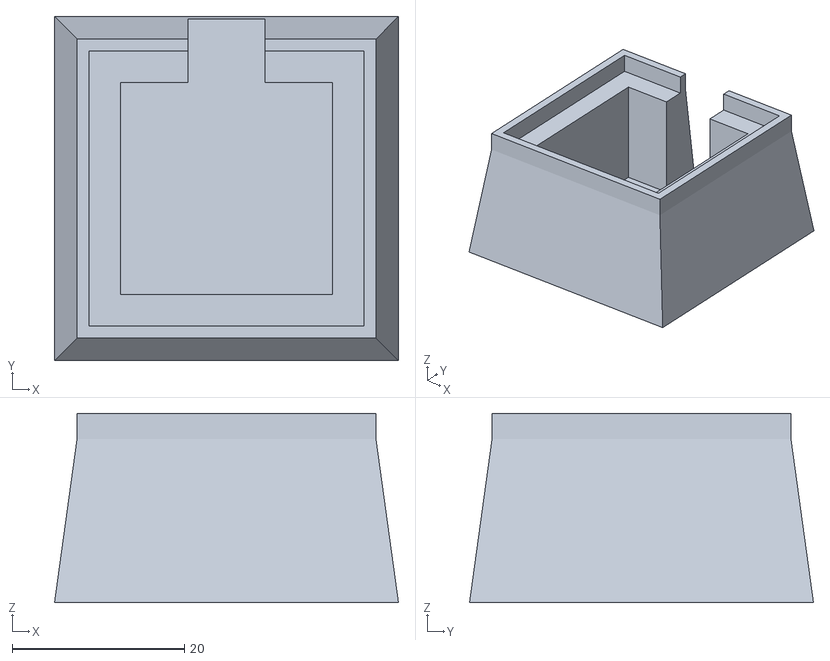
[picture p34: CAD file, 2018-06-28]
CanSat2.0/Code/CanSat_examples/Qwiic_Spectral_Sensor_AS726X-master/Qwiic_Spectral_Sensor_AS726X-master/Enclosure/Programmer/AS726xProgrammerBase.stl
40.0 x 40.0 x 22.0

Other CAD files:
CanSat1.0/Schematics/Model/Arm.ipt
CanSat1.0/Schematics/Model/Battery.ipt
CanSat1.0/Schematics/Model/Camera.ipt
CanSat1.0/Schematics/Model/CanSat.iam
CanSat1.0/Schematics/Model/CanSat.idw
CanSat1.0/Schematics/Model/CanSat.ipn
CanSat1.0/Schematics/Model/Circuit.ipt
CanSat1.0/Schematics/Model/Circuit_2.ipt
CanSat1.0/Schematics/Model/Flight_controler.ipt
CanSat1.0/Schematics/Model/Grove - Oxygen Sensor.ipt
CanSat1.0/Schematics/Model/HGLRC Micro 13A 4in1 BLHeli_S.ipt
CanSat1.0/Schematics/Model/Hull.ipt
CanSat1.0/Schematics/Model/Hull_bottom.ipt
CanSat1.0/Schematics/Model/Hull_middle.ipt
CanSat1.0/Schematics/Model/Hull_top.ipt
CanSat1.0/Schematics/Model/Motor.ipt
CanSat1.0/Schematics/Model/Motor_and_rotor.ipt
CanSat1.0/Schematics/Model/Petri.ipt
CanSat1.0/Schematics/Model/Rotor.ipt
CanSat1.0/Schematics/Model/Scraper.ipt
CanSat1.0/Schematics/Model/Servo.ipt
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

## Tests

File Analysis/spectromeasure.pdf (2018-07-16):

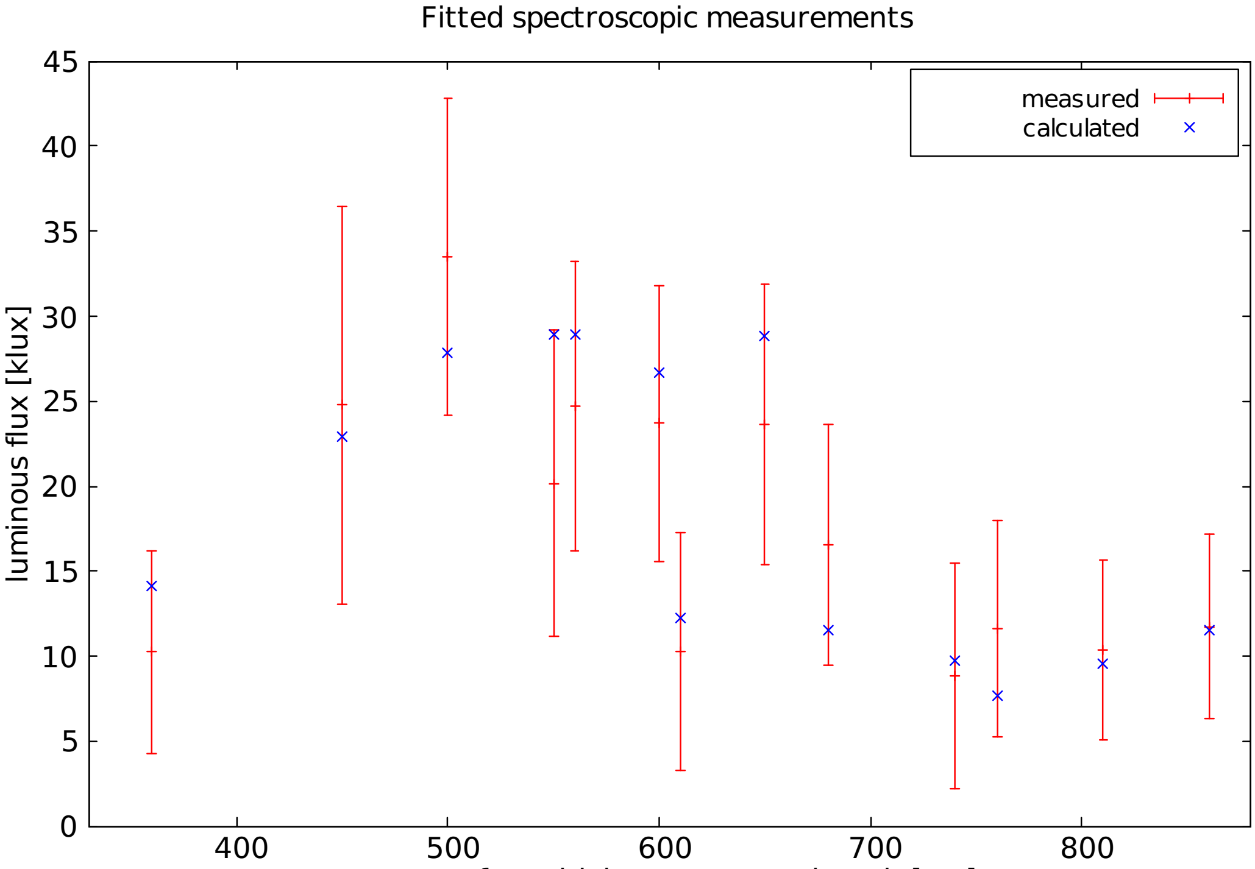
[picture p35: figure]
min; flu; x [klu; Fitted spectroscopic measurements; measured calculated

centre of sensitivity curve wavelength [nm]

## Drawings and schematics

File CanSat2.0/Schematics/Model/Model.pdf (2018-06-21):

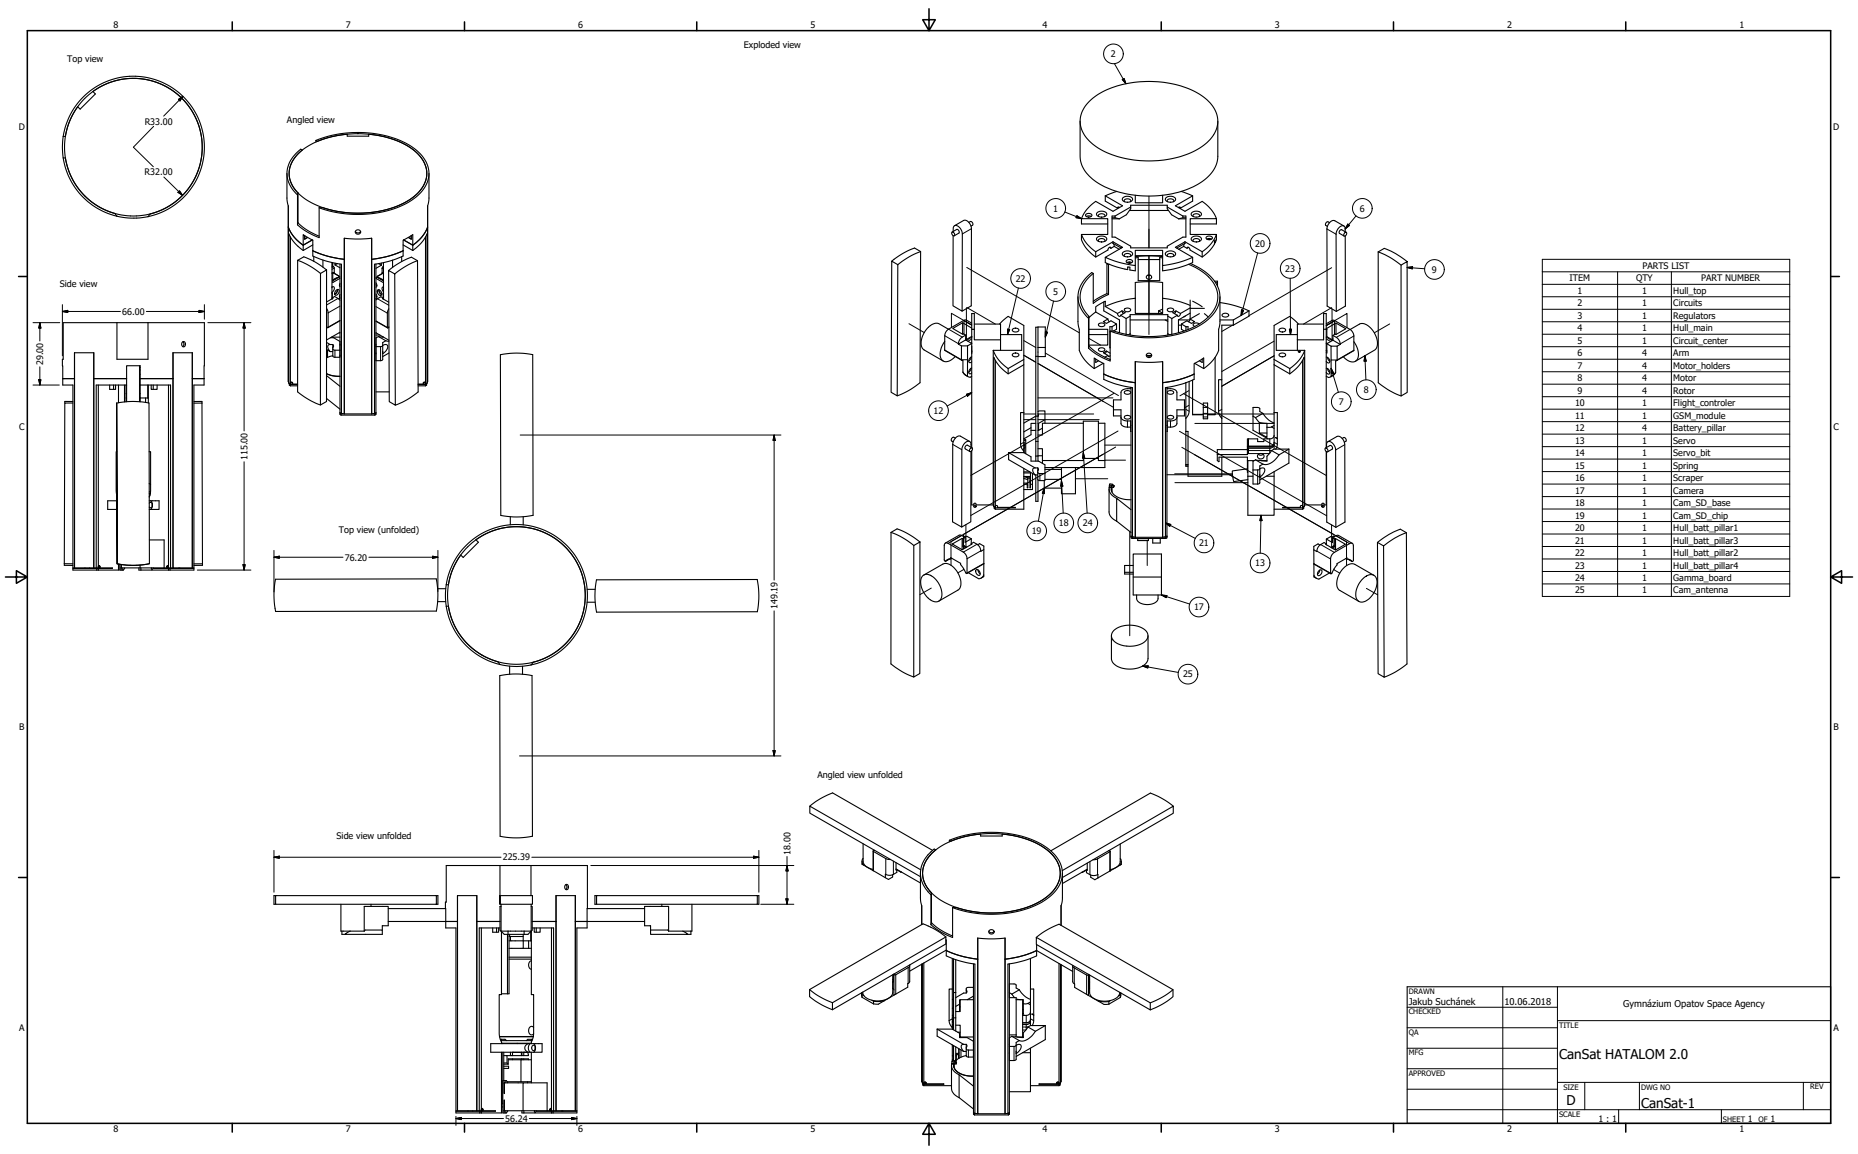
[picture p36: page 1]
TITLE; CanSat HATALOM 2.0; PARTS LIST; Top view; Side view; Angled view; Exploded view

ITEM | QTY | PART NUMBER
1 | 1 | Hull_top
2 | 1 | Circuits
3 | 1 | Regulators
4 | 1 | Hull_main
5 | 1 | Circuit_center
6 | 4 | Arm
7 | 4 | Motor_holders
8 | 4 | Motor
9 | 4 | Rotor
10 | 1 | Flight_controler
11 | 1 | GSM_module
12 | 4 | Battery_pillar
13 | 1 | Servo
14 | 1 | Servo_bit
15 | 1 | Spring
16 | 1 | Scraper
17 | 1 | Camera
18 | 1 | Cam_SD_base
19 | 1 | Cam_SD_chip
20 | 1 | Hull_batt_pillar1
21 | 1 | Hull_batt_pillar3
22 | 1 | Hull_batt_pillar2
23 | 1 | Hull_batt_pillar4
24 | 1 | Gamma_board
25 | 1 | Cam_antenna

Top view (unfolded)

Angled view unfolded

Side view unfolded

DRAWN Jakub Suchánek | 10.06.2018 | Gymnázium Opatov Space Agency

CHECKED

MFG

APPROVED

SIZE D | DWG NO CanSat-1 | REV

SCALE 1 : 1 | | SHEET 1 OF 1

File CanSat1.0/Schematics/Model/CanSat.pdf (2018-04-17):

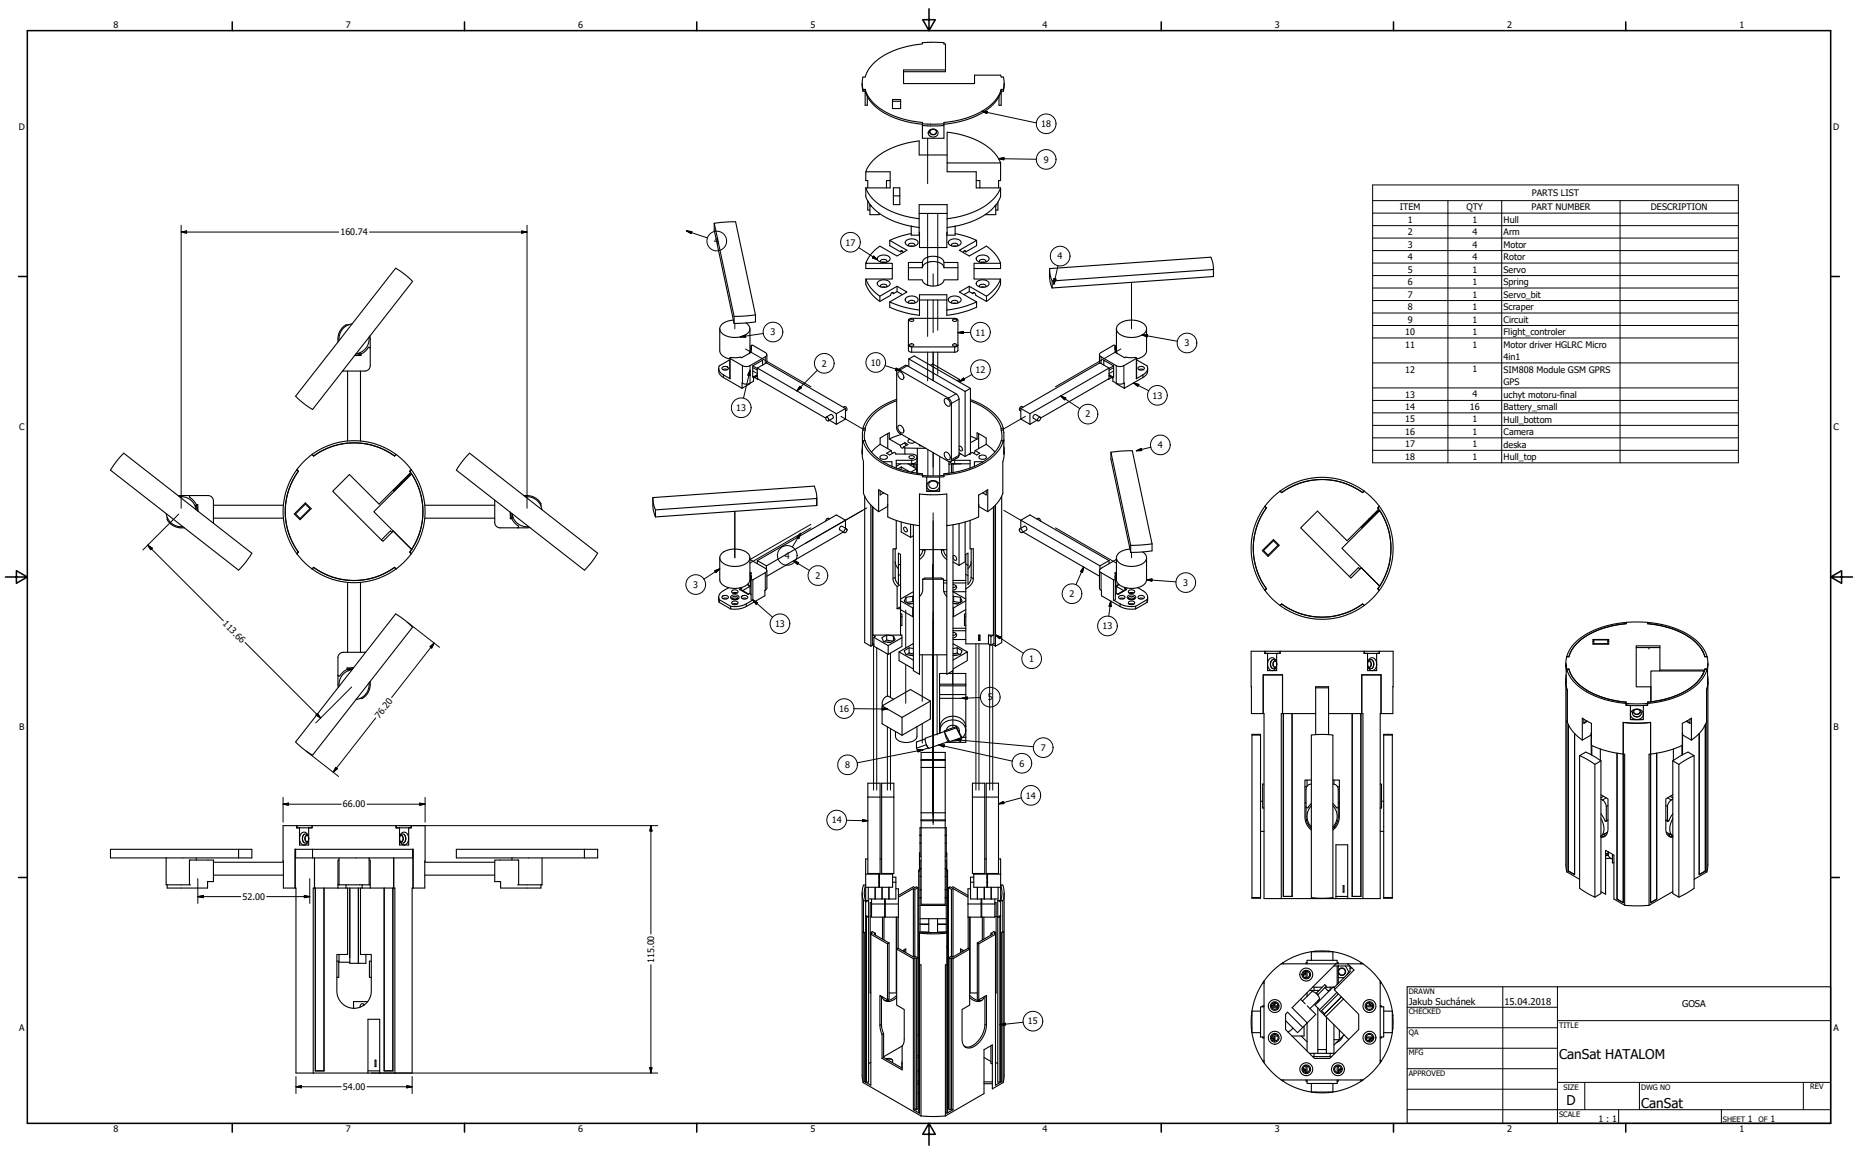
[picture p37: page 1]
TITLE; CanSat HATALOM; PARTS LIST

ITEM | QTY | PART NUMBER | DESCRIPTION
1 | 1 | Hull
2 | 4 | Arm
3 | 4 | Motor
4 | 4 | Rotor
5 | 1 | Servo
6 | 1 | Spring
7 | 1 | Servo_bit
8 | 1 | Scraper
9 | 1 | Circuit
10 | 1 | Flight_controler
11 | 1 | Motor driver HGLRC Micro 4in1

12 | 1 | SIM808 Module GSM GPRS GPS

13 | 4 | uchyt motoru-final
14 | 16 | Battery_small
15 | 1 | Hull_bottom
16 | 1 | Camera
17 | 1 | deska
18 | 1 | Hull_top

DRAWN Jakub Suchánek | 15.04.2018 | GOSA

CHECKED

MFG

APPROVED

SIZE D | DWG NO CanSat | REV

SCALE 1 : 1 | | SHEET 1 OF 1

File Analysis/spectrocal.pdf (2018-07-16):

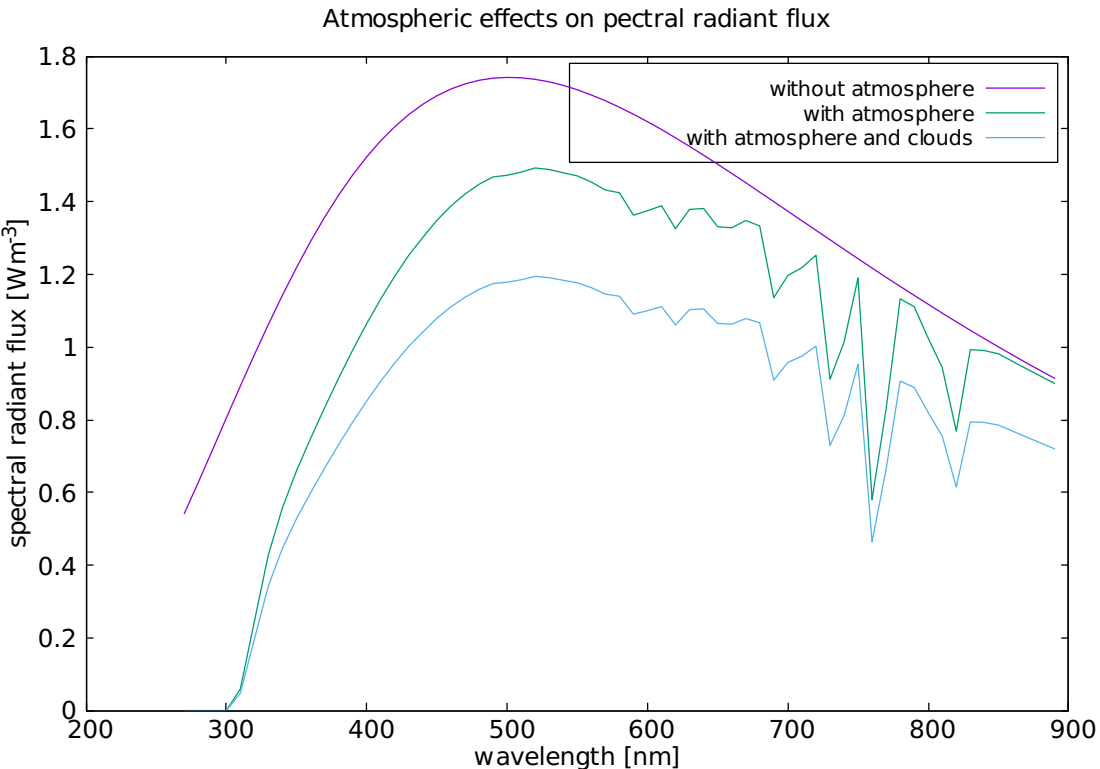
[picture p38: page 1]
dia; flu; wavelength [nm]; without atmosphere with atmosphere

Atmospheric effects on pectral radiant flux

with atmosphere and clouds

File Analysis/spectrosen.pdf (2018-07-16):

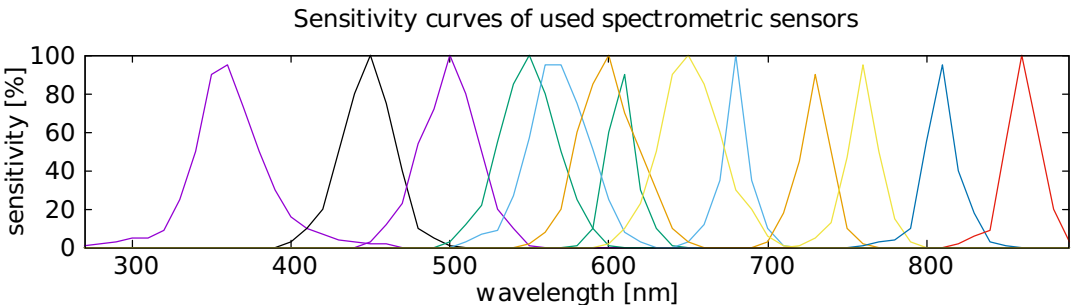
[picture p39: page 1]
sensitivity [%]; ele; sitivit; ric

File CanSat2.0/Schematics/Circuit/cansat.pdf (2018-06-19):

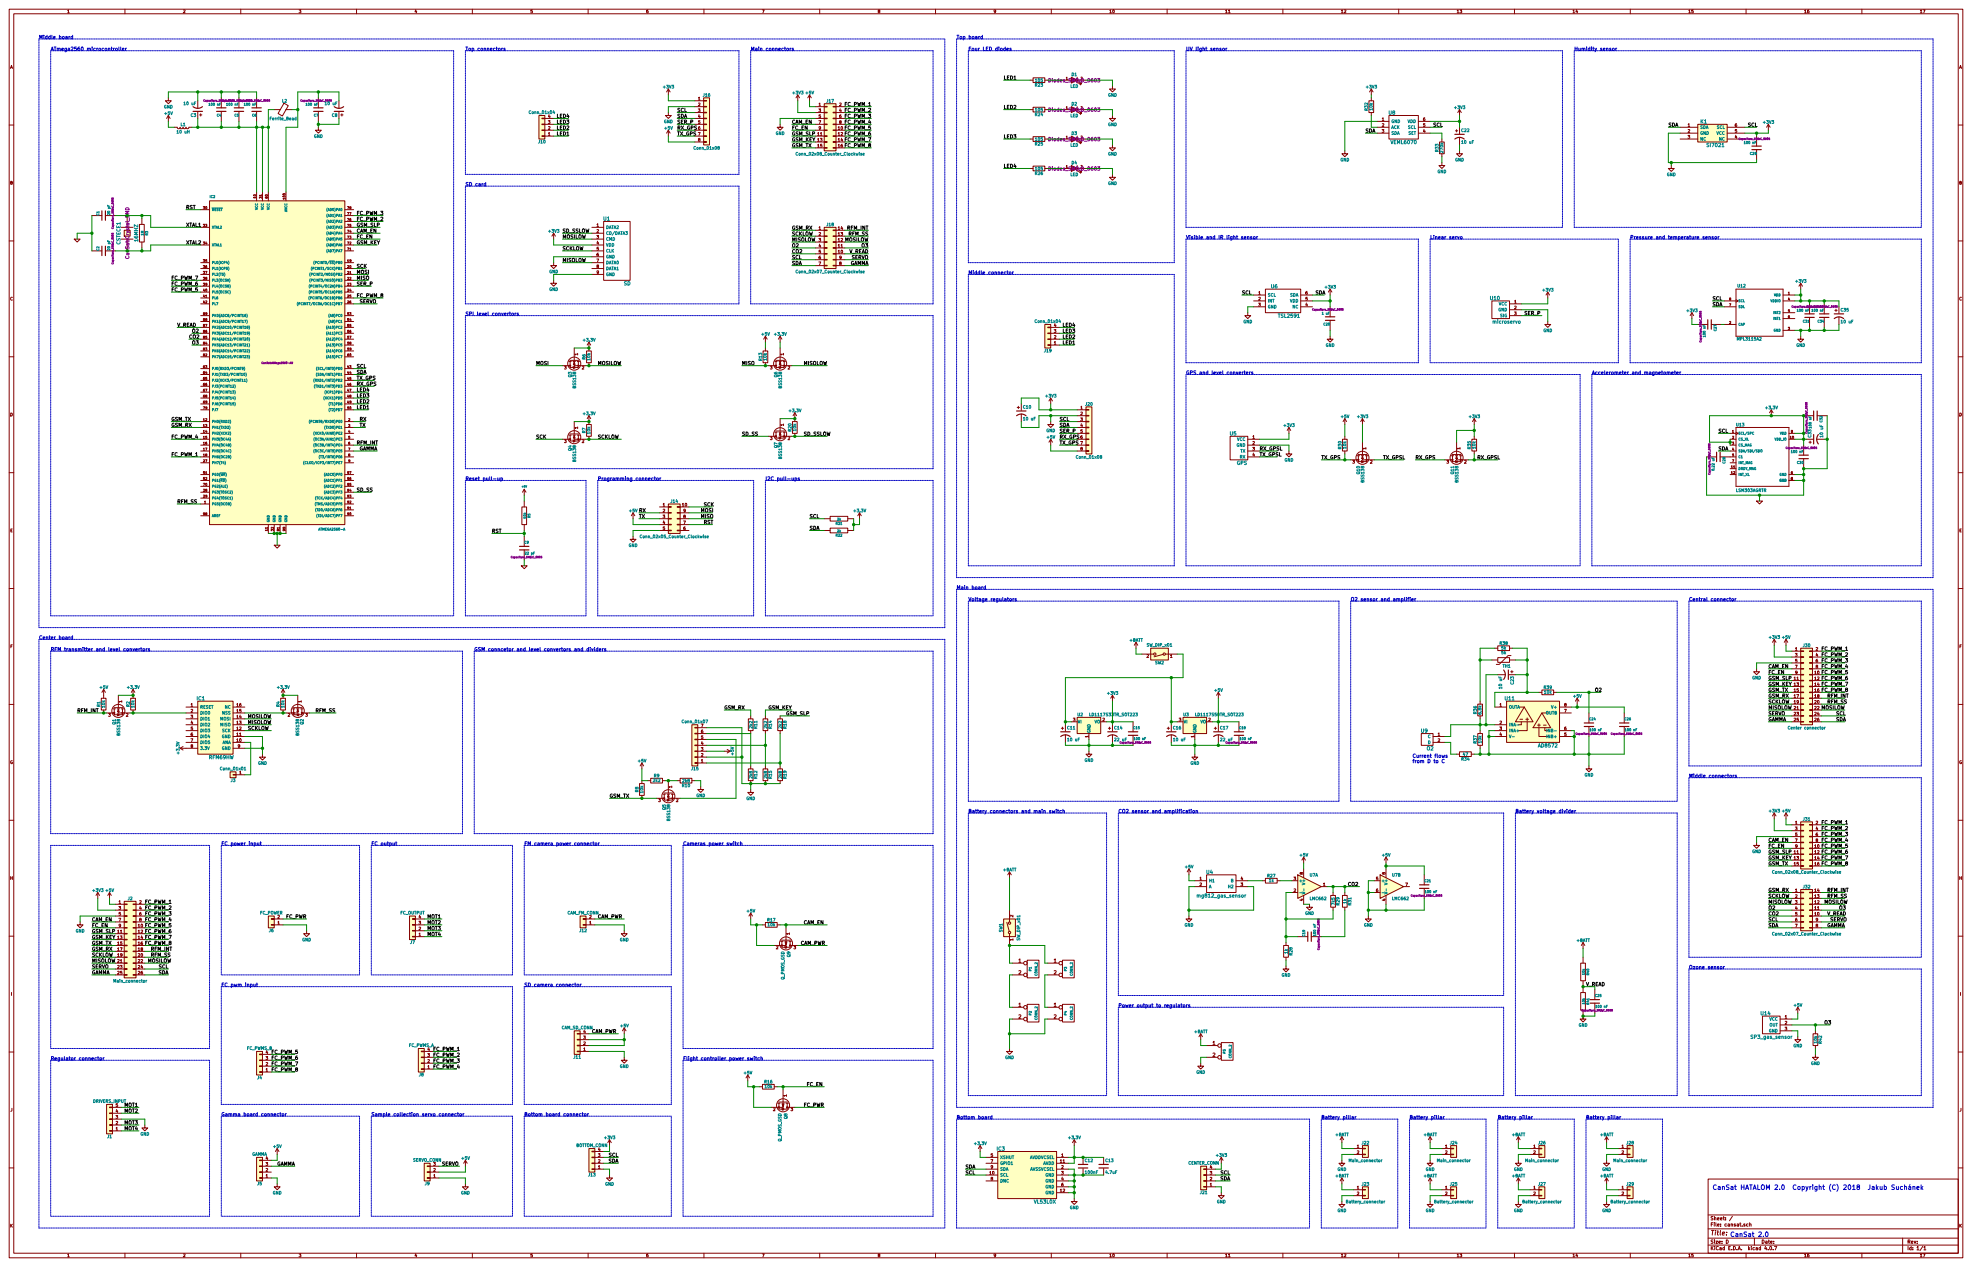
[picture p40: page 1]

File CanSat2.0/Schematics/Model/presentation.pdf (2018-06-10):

1

2

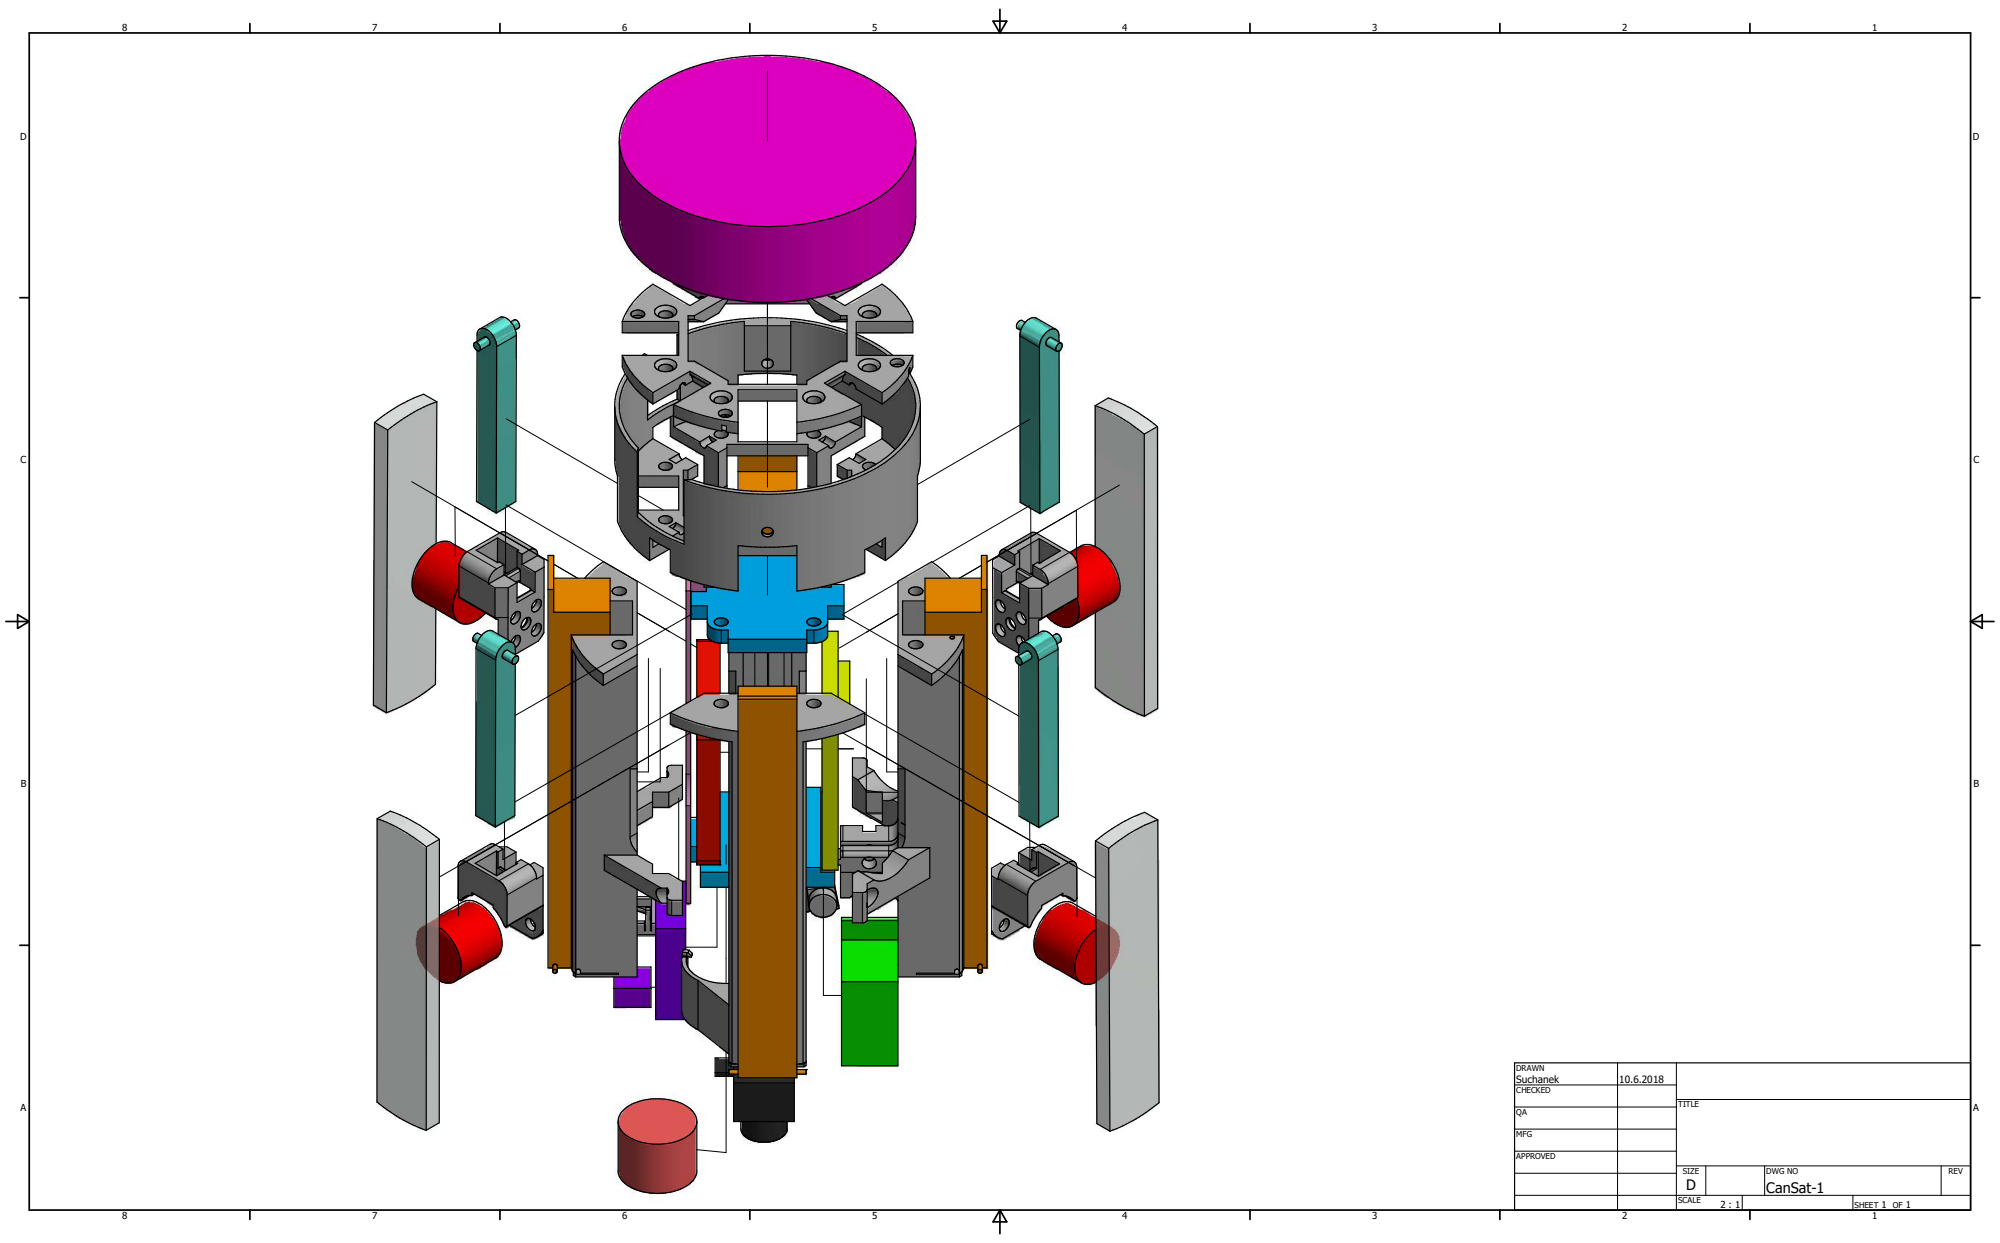
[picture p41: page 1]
SHEET 1 OF 1; DRAWN; CHECKED; MFG; APPROVED; Suchanek; DWG NO CanSat-1; TITLE; SIZE D; SCALE; REV

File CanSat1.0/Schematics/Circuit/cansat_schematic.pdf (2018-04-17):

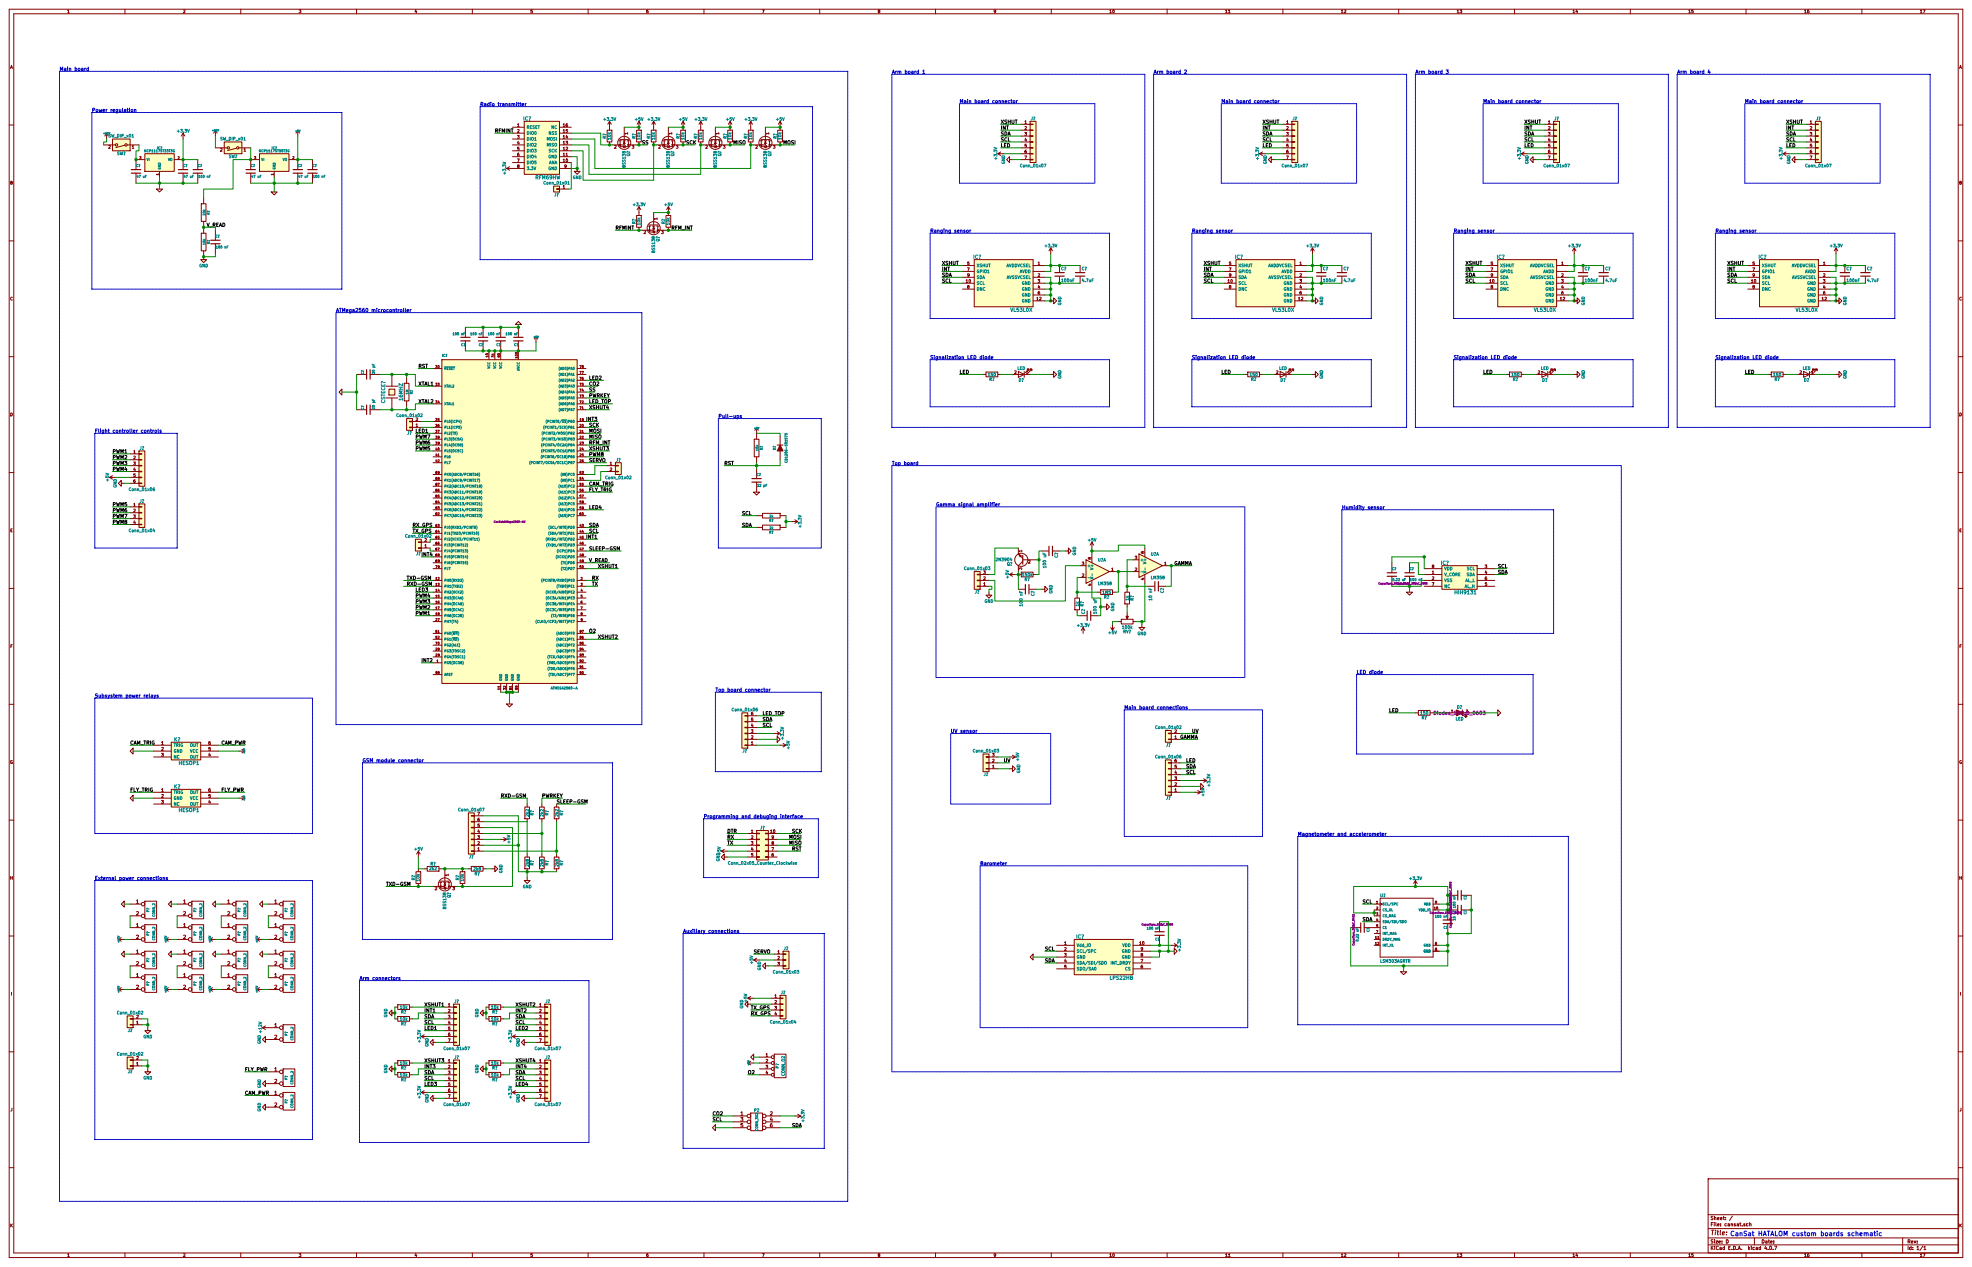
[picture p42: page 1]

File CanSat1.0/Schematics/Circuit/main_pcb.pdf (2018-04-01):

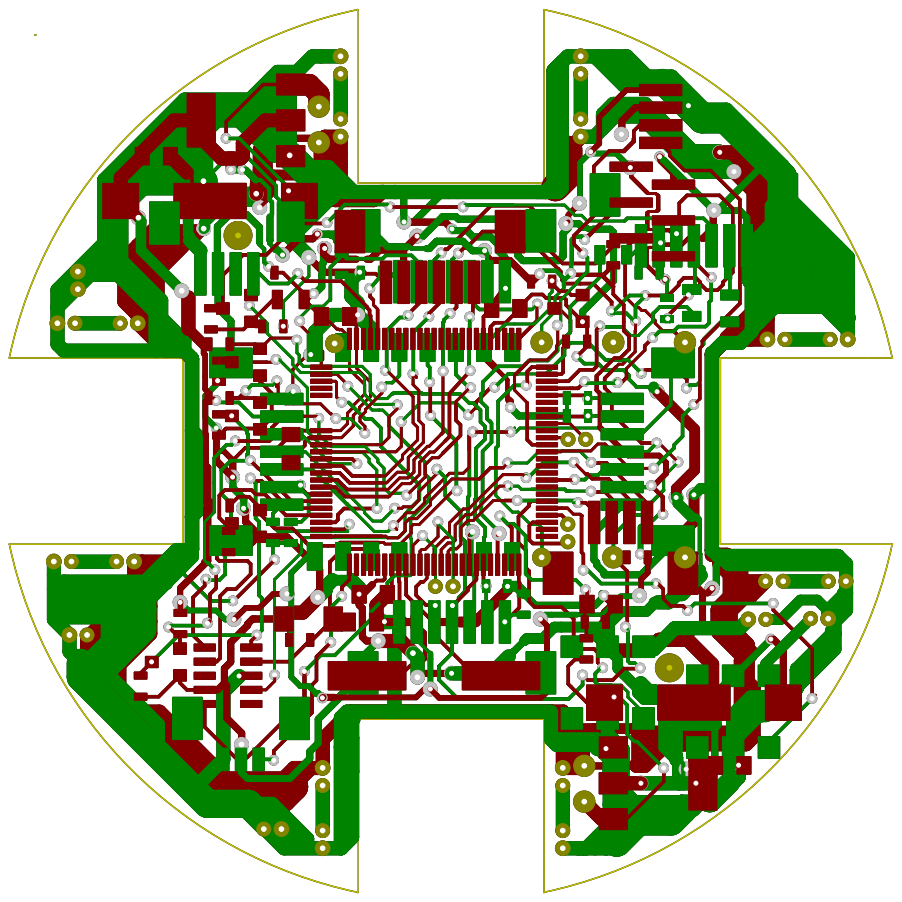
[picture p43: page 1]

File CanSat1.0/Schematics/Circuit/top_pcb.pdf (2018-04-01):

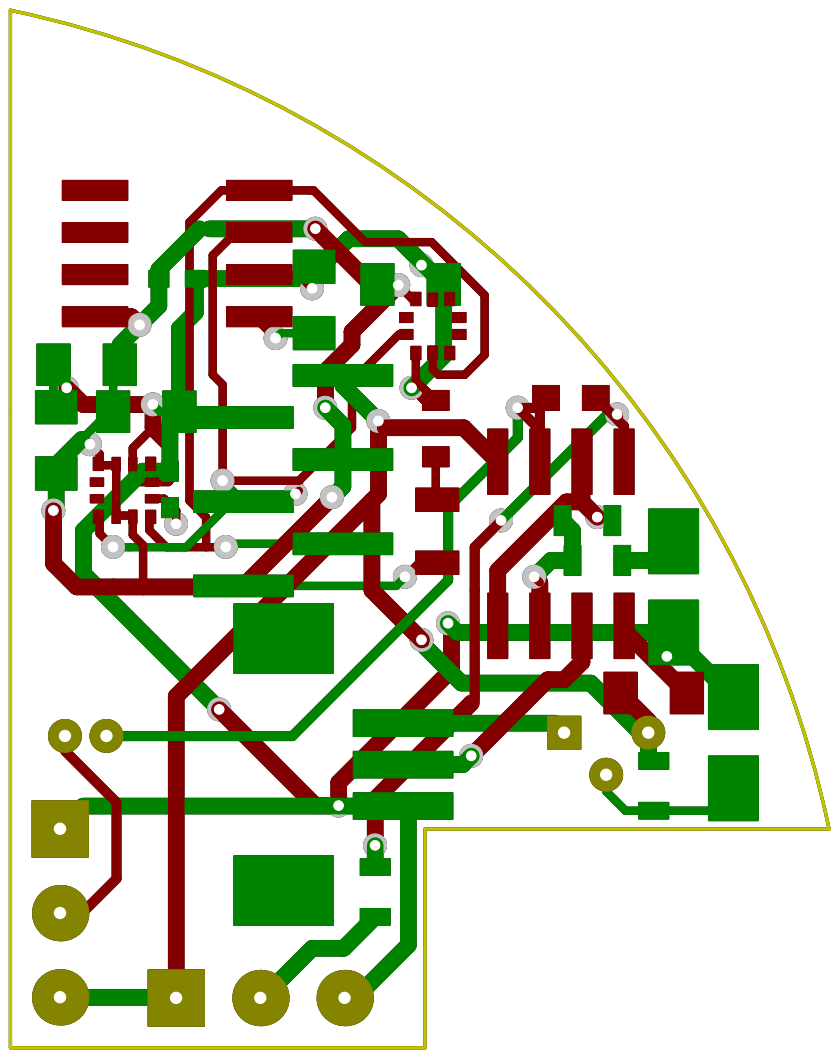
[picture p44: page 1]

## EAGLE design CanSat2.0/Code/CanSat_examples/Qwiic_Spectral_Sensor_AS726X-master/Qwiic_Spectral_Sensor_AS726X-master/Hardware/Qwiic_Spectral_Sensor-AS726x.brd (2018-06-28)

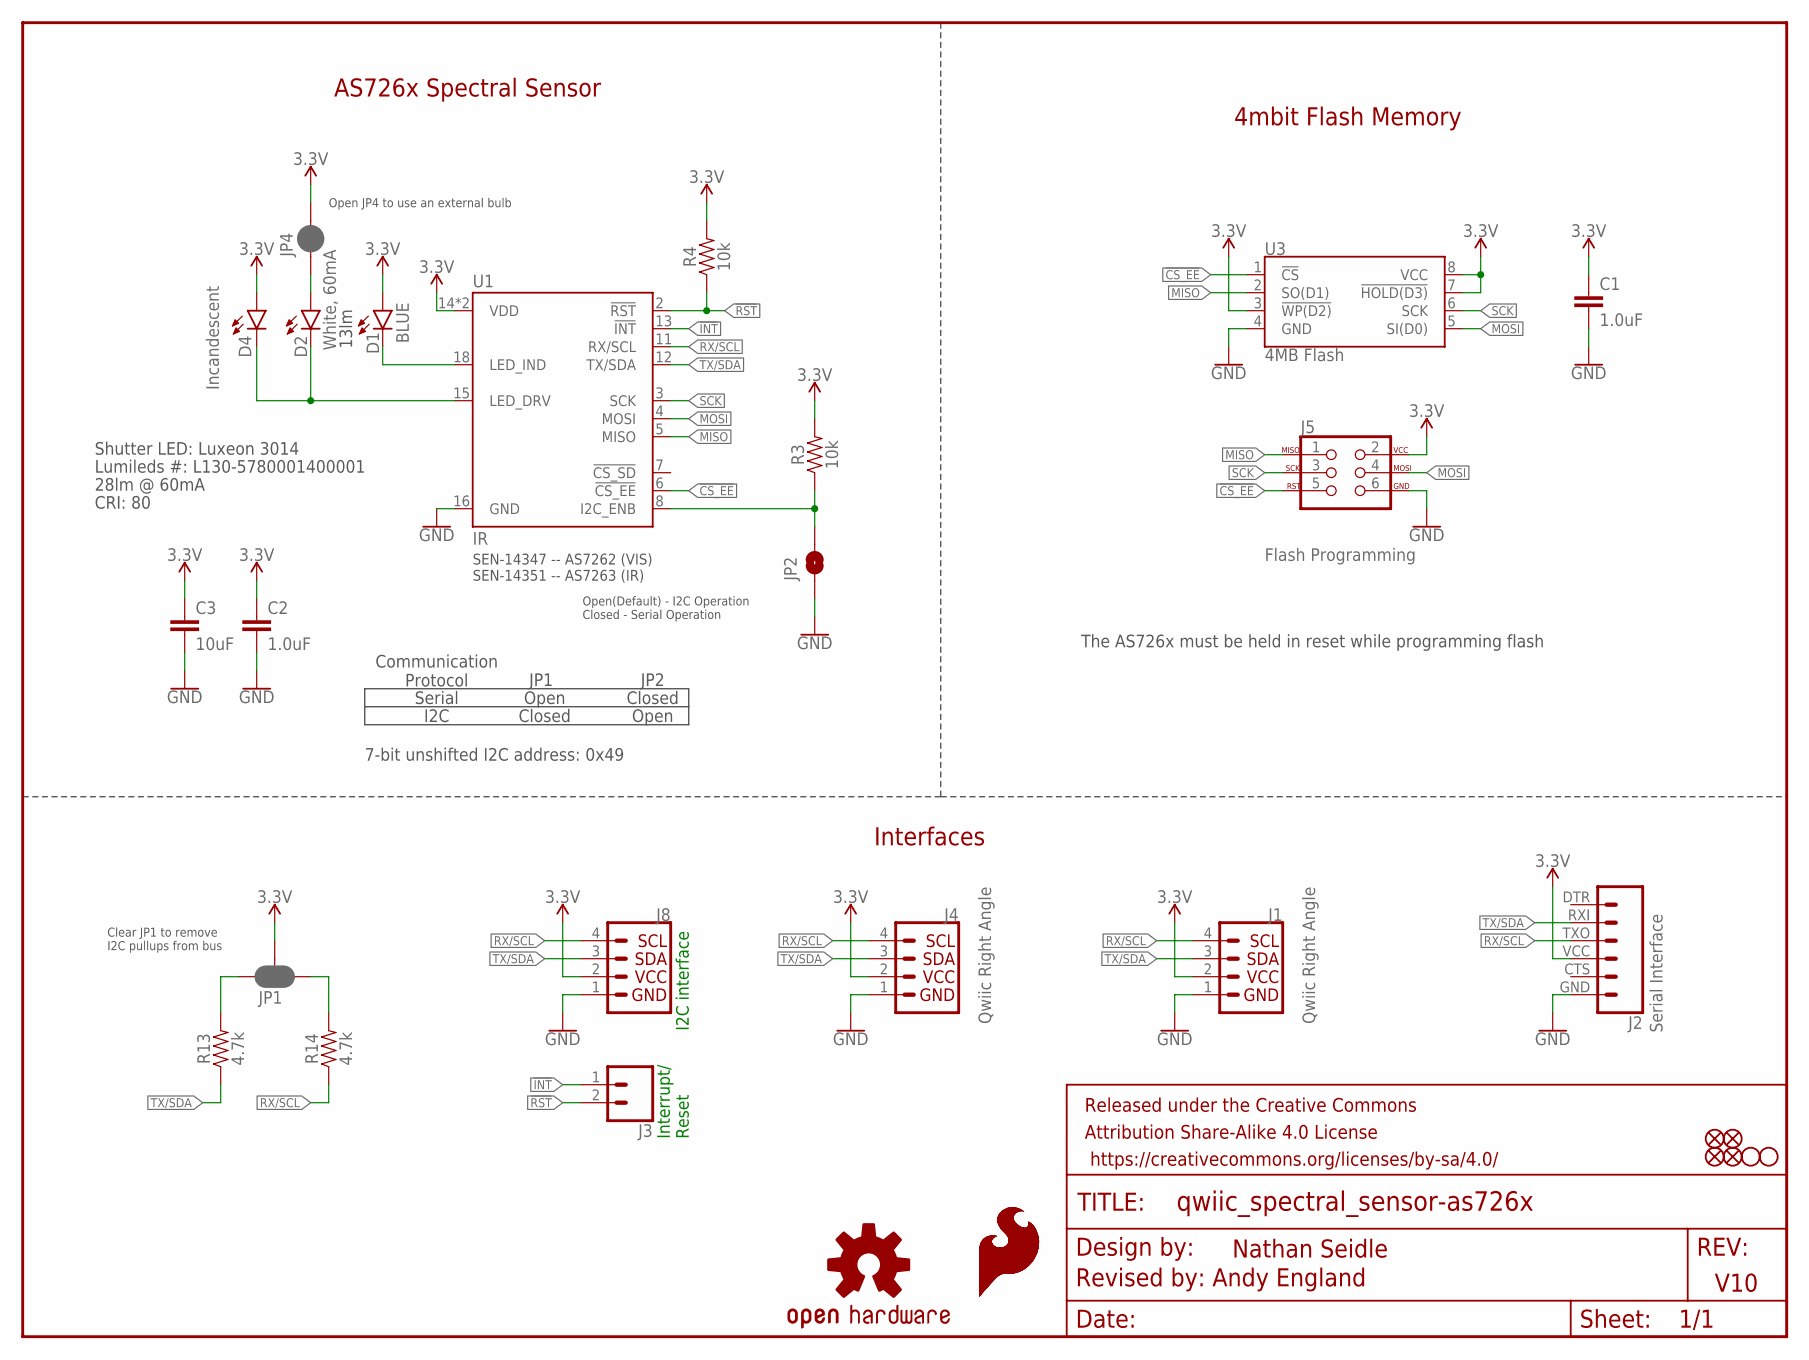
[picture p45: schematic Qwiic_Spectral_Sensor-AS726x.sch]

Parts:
C1, C2: 1.0uF; 0603
C3: 10uF; 0603
D1: BLUE; LED-0603
D2: White, 60mA; SUPER_BRIGHT_SMD_LED_3014
D4: Incandescent; LED_5MM_NOSILK
FD1, FD2, FD3, FD4: FIDUCIAL1X2; FIDUCIAL-1X2
FRAME1: FRAME-LETTER; CREATIVE_COMMONS
H2, H4: STAND-OFF
J1, J4: Qwiic Right Angle; 1X04_1MM_RA
J2: Serial Interface; FTDI_BASIC
J3: CONN_021X02_NO_SILK; 1X02_NO_SILK
J5: Flash Programming; 2X3_TEST_POINTS
J8: I2C_STANDARD_NO_SILK; 1X04_NO_SILK
JP1: JUMPER-SMT_3_2-NC_PASTE_SILK; SMT-JUMPER_3_2-NC_PASTE_SILK
JP2: JUMPER-SMT_2_NO_SILK; SMT-JUMPER_2_NO_SILK
JP4: JUMPER-SMT_2_NC_PASTE_NO-SILK; SMT-JUMPER_2_NC_PASTE_NO-SILK
LOGO1, LOGO2: SFE_LOGO_FLAME.2_INCH; SFE_LOGO_FLAME_.2
LOGO4: OSHW-LOGOS; OSHW-LOGO-S
R3, R4: 10k; 0603
R13, R14: 4.7k; 0603
U1: IR; LGA20
U3: 4MB Flash; SO08

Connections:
3.3V: C1.1, C2.1, C3.1, D1.A, D4.A, J1.2, J2.VCC (4), J4.2, J5.2, J8.2, JP1.2, JP4.2, R3.2, R4.2, U1.14 (VDD), U1.17 (VDD), U3.3 (!WP(D2)), U3.7 (!HOLD(D3)), U3.8 (VCC)
!CS_EE: J5.5, U1.6 (!CS_EE), U3.1 (!CS)
!INT: J3.1, U1.13 (!INT)
!RST: J3.2, R4.1, U1.2 (!RST)
GND: C1.2, C2.2, C3.2, J1.1, J2.GND (6), J4.1, J5.6, J8.1, JP2.1, U1.16 (GND), U3.4 (GND)
LED_DRV: D2.C, D4.K (C), U1.15 (LED_DRV)
MISO: J5.1, U1.5 (MISO), U3.2 (SO(D1))
MOSI: J5.4, U1.4 (MOSI), U3.5 (SI(D0))
unnamed: JP2.2, R3.1, U1.8 (I2C_ENB)
unnamed: D1.C, U1.18 (LED_IND)
unnamed: JP1.3, R13.2
unnamed: JP1.1, R14.2
unnamed: D2.A, JP4.1
RX/SCL: J1.4, J2.TXO (3), J4.4, J8.4, R14.1, U1.11 (RX/SCL)
SCK: J5.3, U1.3 (SCK), U3.6 (SCK)
TX/SDA: J1.3, J2.RXI (2), J4.3, J8.3, R13.1, U1.12 (TX/SDA)

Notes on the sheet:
AS726x Spectral Sensor
Open(Default) - I2C Operation Closed - Serial Operation
Clear JP1 to remove I2C pullups from bus
V10
Nathan Seidle
4mbit Flash Memory
Interfaces
The AS726x must be held in reset while programming flash
Open JP4 to use an external bulb
Serial
JP1
JP2
Open
Closed
Communication Protocol
I2C
13lm
Lumileds #: L130-5780001400001
Shutter LED: Luxeon 3014
28lm @ 60mA
CRI: 80
7-bit unshifted I2C address: 0x49
I2C interface
Interrupt/ Reset
Revised by: Andy England
SEN-14347 -- AS7262 (VIS) SEN-14351 -- AS7263 (IR)

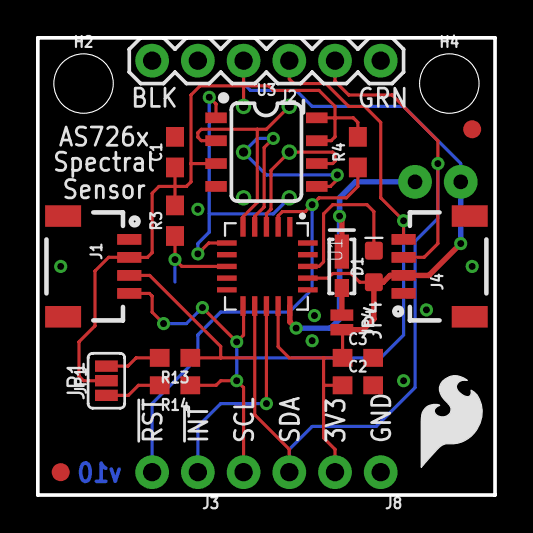
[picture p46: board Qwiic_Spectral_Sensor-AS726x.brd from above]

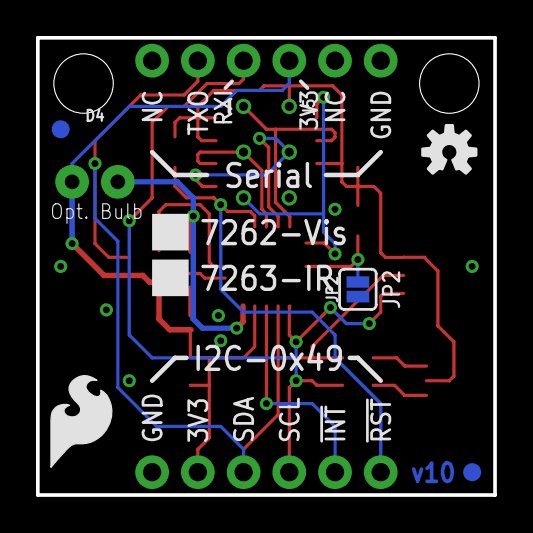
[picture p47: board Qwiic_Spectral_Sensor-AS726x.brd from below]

Board: 2 copper layers, 25.4 x 25.4 mm, 32 parts (7 on the bottom side), 16 nets.

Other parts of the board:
U$2: REVISION

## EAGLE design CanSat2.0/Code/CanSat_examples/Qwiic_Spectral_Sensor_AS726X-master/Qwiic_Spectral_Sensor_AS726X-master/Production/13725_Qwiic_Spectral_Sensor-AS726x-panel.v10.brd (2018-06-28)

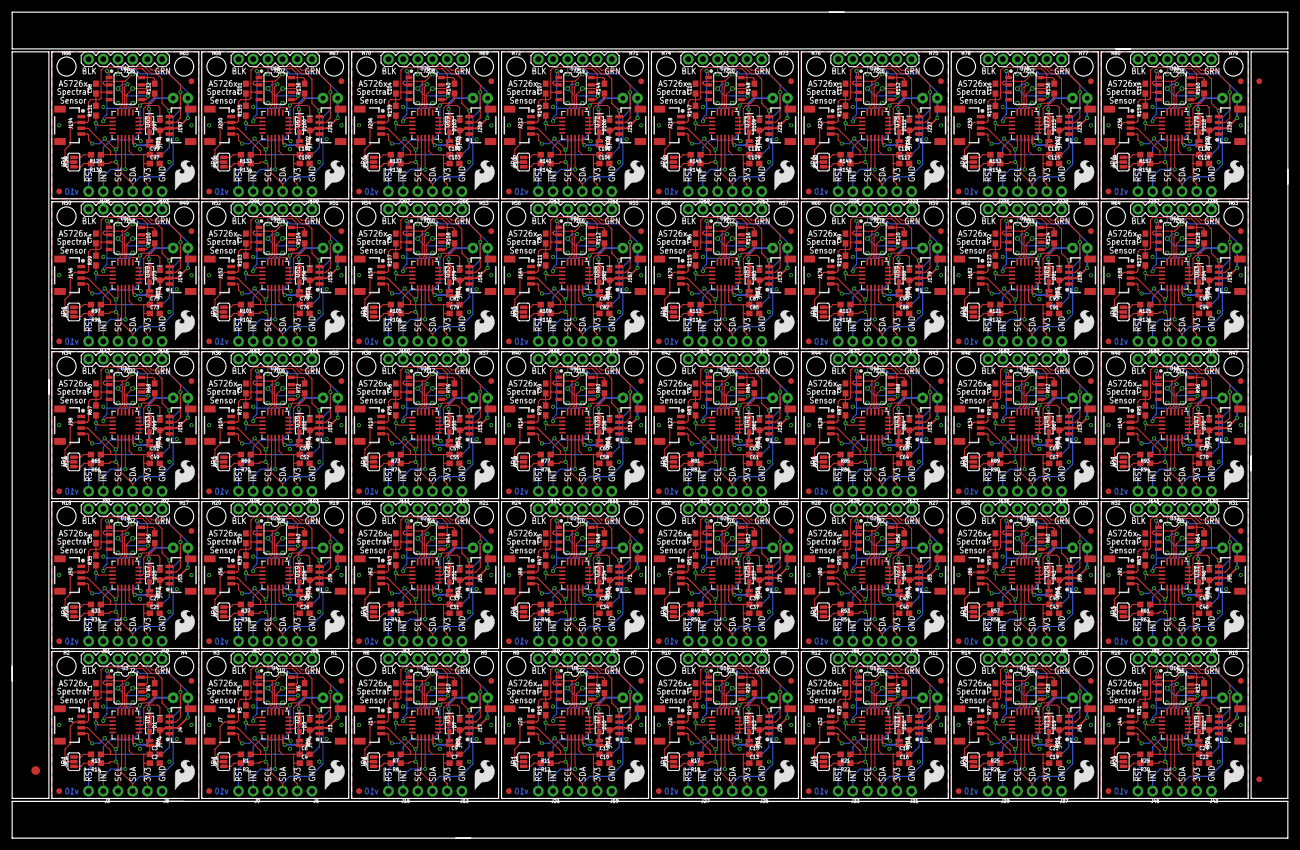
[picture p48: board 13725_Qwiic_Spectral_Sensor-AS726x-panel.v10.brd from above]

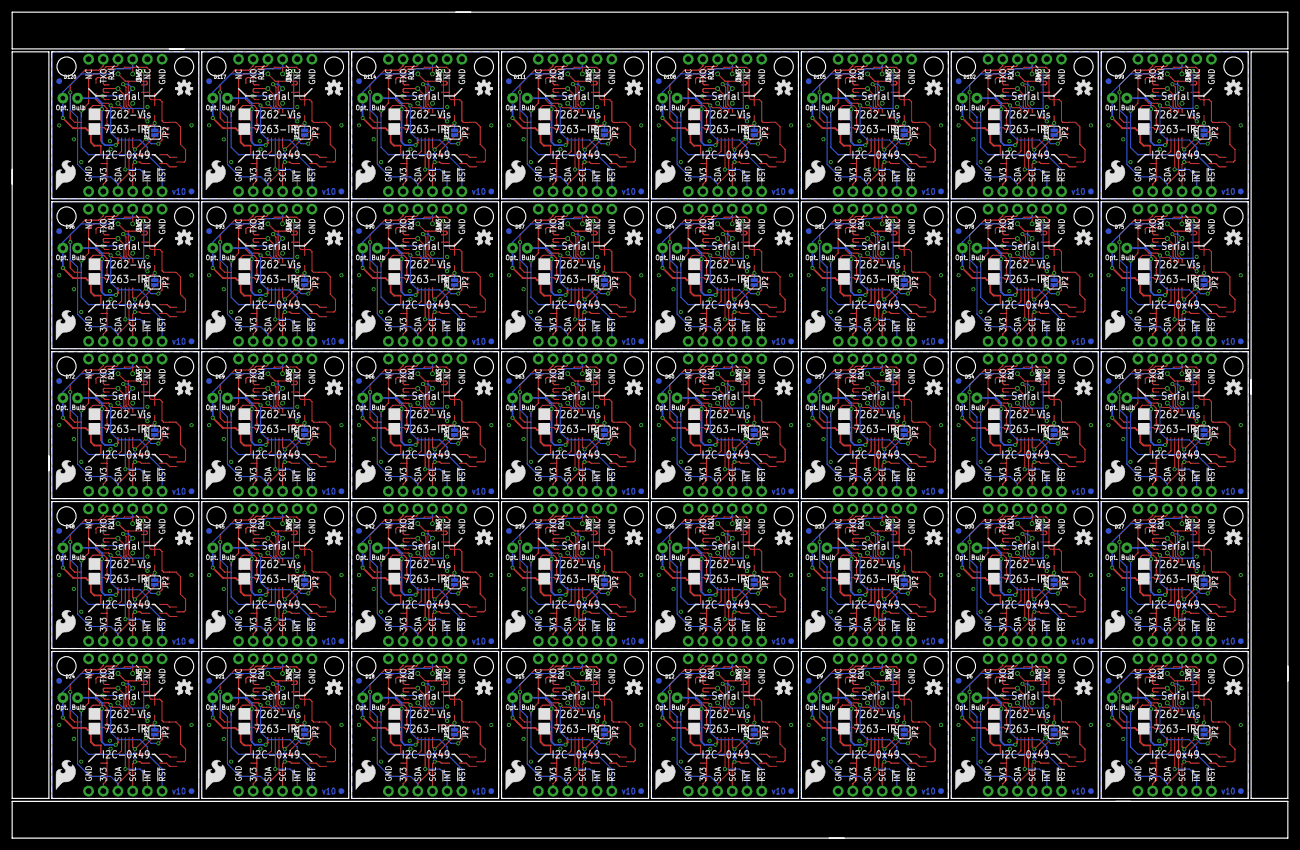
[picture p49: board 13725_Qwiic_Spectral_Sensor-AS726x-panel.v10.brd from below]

Board: 2 copper layers, 220.5 x 142.7 mm, 1203 parts (280 on the bottom side), 640 nets.

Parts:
C1, C2, C4, C5, C7, C8, C10, C11, C13, C14, C16, C17, C19, C20, C22, C23, C25, C26, C28, C29, C31, C32, C34, C35, C37, C38, C40, C41, C43, C44, C46, C47, C49, C50, C52, C53, C55, C56, C58, C59, C61, C62, C64, C65, C67, C68, C70, C71, C73, C74, C76, C77, C79, C80, C82, C83, C85, C86, C88, C89, C91, C92, C94, C95, C97, C98, C100, C101, C103, C104, C106, C107, C109, C110, C112, C113, C115, C116, C118, C119: 1.0uF; 0603
C3, C6, C9, C12, C15, C18, C21, C24, C27, C30, C33, C36, C39, C42, C45, C48, C51, C54, C57, C60, C63, C66, C69, C72, C75, C78, C81, C84, C87, C90, C93, C96, C99, C102, C105, C108, C111, C114, C117, C120: 10uF; 0603
D1, D3, D7, D10, D13, D16, D19, D22, D25, D28, D31, D34, D37, D40, D43, D46, D49, D52, D55, D58, D61, D64, D67, D70, D73, D76, D79, D82, D85, D88, D91, D94, D97, D100, D103, D106, D109, D112, D115, D118: BLUE; LED-0603
D2, D5, D8, D11, D14, D17, D20, D23, D26, D29, D32, D35, D38, D41, D44, D47, D50, D53, D56, D59, D62, D65, D68, D71, D74, D77, D80, D83, D86, D89, D92, D95, D98, D101, D104, D107, D110, D113, D116, D119: White, 60mA; SUPER_BRIGHT_SMD_LED_3014
D4, D6, D9, D12, D15, D18, D21, D24, D27, D30, D33, D36, D39, D42, D45, D48, D51, D54, D57, D60, D63, D66, D69, D72, D75, D78, D81, D84, D87, D90, D93, D96, D99, D102, D105, D108, D111, D114, D117, D120: Incandescent; LED_5MM_NOSILK
E$1: FIDUCIAL-1.5X3
E$7, E$8: FIDUCIAL-1X2
FD1, FD2, FD3, FD4, FD5, FD6, FD7, FD8, FD9, FD10, FD11, FD12, FD13, FD14, FD15, FD16, FD17, FD18, FD19, FD20, FD21, FD22, FD23, FD24, FD25, FD26, FD27, FD28, FD29, FD30, FD31, FD32, FD33, FD34, FD35, FD36, FD37, FD38, FD39, FD40, FD41, FD42, FD43, FD44, FD45, FD46, FD47, FD48, FD49, FD50, FD51, FD52, FD53, FD54, FD55, FD56, FD57, FD58, FD59, FD60, FD61, FD62, FD63, FD64, FD65, FD66, FD67, FD68, FD69, FD70, FD71, FD72, FD73, FD74, FD75, FD76, FD77, FD78, FD79, FD80, FD81, FD82, FD83, FD84, FD85, FD86, FD87, FD88, FD89, FD90, FD91, FD92, FD93, FD94, FD95, FD96, FD97, FD98, FD99, FD100, FD101, FD102, FD103, FD104, FD105, FD106, FD107, FD108, FD109, FD110, FD111, FD112, FD113, FD114, FD115, FD116, FD117, FD118, FD119, FD120, FD121, FD122, FD123, FD124, FD125, FD126, FD127, FD128, FD129, FD130, FD131, FD132, FD133, FD134, FD135, FD136, FD137, FD138, FD139, FD140, FD141, FD142, FD143, FD144, FD145, FD146, FD147, FD148, FD149, FD150, FD151, FD152, FD153, FD154, FD155, FD156, FD157, FD158, FD159, FD160: FIDUCIAL1X2; FIDUCIAL-1X2
H1, H2, H3, H4, H5, H6, H7, H8, H9, H10, H11, H12, H13, H14, H15, H16, H17, H18, H19, H20, H21, H22, H23, H24, H25, H26, H27, H28, H29, H30, H31, H32, H33, H34, H35, H36, H37, H38, H39, H40, H41, H42, H43, H44, H45, H46, H47, H48, H49, H50, H51, H52, H53, H54, H55, H56, H57, H58, H59, H60, H61, H62, H63, H64, H65, H66, H67, H68, H69, H70, H71, H72, H73, H74, H75, H76, H77, H78, H79, H80: STAND-OFF
J1, J4, J7, J11, J14, J17, J20, J23, J26, J29, J32, J35, J38, J41, J44, J47, J50, J53, J56, J59, J62, J65, J68, J71, J74, J77, J80, J83, J86, J89, J92, J95, J98, J101, J104, J107, J110, J113, J116, J119, J122, J125, J128, J131, J134, J137, J140, J143, J146, J149, J152, J155, J158, J161, J164, J167, J170, J173, J176, J179, J182, J185, J188, J191, J194, J197, J200, J203, J206, J209, J212, J215, J218, J221, J224, J227, J230, J233, J236, J239: Qwiic Right Angle; 1X04_1MM_RA
J2, J10, J16, J22, J28, J34, J40, J46, J52, J58, J64, J70, J76, J82, J88, J94, J100, J106, J112, J118, J124, J130, J136, J142, J148, J154, J160, J166, J172, J178, J184, J190, J196, J202, J208, J214, J220, J226, J232, J238: Serial Interface; FTDI_BASIC
J3, J9, J15, J21, J27, J33, J39, J45, J51, J57, J63, J69, J75, J81, J87, J93, J99, J105, J111, J117, J123, J129, J135, J141, J147, J153, J159, J165, J171, J177, J183, J189, J195, J201, J207, J213, J219, J225, J231, J237: 1X02_NO_SILK
J5, J12, J18, J24, J30, J36, J42, J48, J54, J60, J66, J72, J78, J84, J90, J96, J102, J108, J114, J120, J126, J132, J138, J144, J150, J156, J162, J168, J174, J180, J186, J192, J198, J204, J210, J216, J222, J228, J234, J240: Flash Programming; 2X3_TEST_POINTS
J6, J8, J13, J19, J25, J31, J37, J43, J49, J55, J61, J67, J73, J79, J85, J91, J97, J103, J109, J115, J121, J127, J133, J139, J145, J151, J157, J163, J169, J175, J181, J187, J193, J199, J205, J211, J217, J223, J229, J235: 1X04_NO_SILK
JP1, JP5, JP8, JP11, JP14, JP17, JP20, JP23, JP26, JP29, JP32, JP35, JP38, JP41, JP44, JP47, JP50, JP53, JP56, JP59, JP62, JP65, JP68, JP71, JP74, JP77, JP80, JP83, JP86, JP89, JP92, JP95, JP98, JP101, JP104, JP107, JP110, JP113, JP116, JP119: SMT-JUMPER_3_2-NC_PASTE_SILK
JP2, JP3, JP7, JP10, JP13, JP16, JP19, JP22, JP25, JP28, JP31, JP34, JP37, JP40, JP43, JP46, JP49, JP52, JP55, JP58, JP61, JP64, JP67, JP70, JP73, JP76, JP79, JP82, JP85, JP88, JP91, JP94, JP97, JP100, JP103, JP106, JP109, JP112, JP115, JP118: SMT-JUMPER_2_NO_SILK
JP4, JP6, JP9, JP12, JP15, JP18, JP21, JP24, JP27, JP30, JP33, JP36, JP39, JP42, JP45, JP48, JP51, JP54, JP57, JP60, JP63, JP66, JP69, JP72, JP75, JP78, JP81, JP84, JP87, JP90, JP93, JP96, JP99, JP102, JP105, JP108, JP111, JP114, JP117, JP120: SMT-JUMPER_2_NC_PASTE_NO-SILK
LOGO1, LOGO2, LOGO5, LOGO6, LOGO8, LOGO9, LOGO11, LOGO12, LOGO14, LOGO15, LOGO17, LOGO18, LOGO20, LOGO21, LOGO23, LOGO24, LOGO26, LOGO27, LOGO29, LOGO30, LOGO32, LOGO33, LOGO35, LOGO36, LOGO38, LOGO39, LOGO41, LOGO42, LOGO44, LOGO45, LOGO47, LOGO48, LOGO50, LOGO51, LOGO53, LOGO54, LOGO56, LOGO57, LOGO59, LOGO60, LOGO62, LOGO63, LOGO65, LOGO66, LOGO68, LOGO69, LOGO71, LOGO72, LOGO74, LOGO75, LOGO77, LOGO78, LOGO80, LOGO81, LOGO83, LOGO84, LOGO86, LOGO87, LOGO89, LOGO90, LOGO92, LOGO93, LOGO95, LOGO96, LOGO98, LOGO99, LOGO101, LOGO102, LOGO104, LOGO105, LOGO107, LOGO108, LOGO110, LOGO111, LOGO113, LOGO114, LOGO116, LOGO117, LOGO119, LOGO120: SFE_LOGO_FLAME.2_INCH; SFE_LOGO_FLAME_.2
LOGO3, LOGO4, LOGO7, LOGO10, LOGO13, LOGO16, LOGO19, LOGO22, LOGO25, LOGO28, LOGO31, LOGO34, LOGO37, LOGO40, LOGO43, LOGO46, LOGO49, LOGO52, LOGO55, LOGO58, LOGO61, LOGO64, LOGO67, LOGO70, LOGO73, LOGO76, LOGO79, LOGO82, LOGO85, LOGO88, LOGO91, LOGO94, LOGO97, LOGO100, LOGO103, LOGO106, LOGO109, LOGO112, LOGO115, LOGO118: OSHW-LOGOS; OSHW-LOGO-S
R1, R2, R7, R8, R11, R12, R13, R14, R17, R18, R21, R22, R25, R26, R29, R30, R33, R34, R37, R38, R41, R42, R45, R46, R49, R50, R53, R54, R57, R58, R61, R62, R65, R66, R69, R70, R73, R74, R77, R78, R81, R82, R85, R86, R89, R90, R93, R94, R97, R98, R101, R102, R105, R106, R109, R110, R113, R114, R117, R118, R121, R122, R125, R126, R129, R130, R133, R134, R137, R138, R141, R142, R145, R146, R149, R150, R153, R154, R157, R158: 4.7k; 0603
R3, R4, R5, R6, R9, R10, R15, R16, R19, R20, R23, R24, R27, R28, R31, R32, R35, R36, R39, R40, R43, R44, R47, R48, R51, R52, R55, R56, R59, R60, R63, R64, R67, R68, R71, R72, R75, R76, R79, R80, R83, R84, R87, R88, R91, R92, R95, R96, R99, R100, R103, R104, R107, R108, R111, R112, R115, R116, R119, R120, R123, R124, R127, R128, R131, R132, R135, R136, R139, R140, R143, R144, R147, R148, R151, R152, R155, R156, R159, R160: 10k; 0603
U1, U2, U5, U7, U9, U11, U13, U15, U17, U19, U21, U23, U25, U27, U29, U31, U33, U35, U37, U39, U41, U43, U45, U47, U49, U51, U53, U55, U57, U59, U61, U63, U65, U67, U69, U71, U73, U75, U77, U79: IR; LGA20
U3, U4, U6, U8, U10, U12, U14, U16, U18, U20, U22, U24, U26, U28, U30, U32, U34, U36, U38, U40, U42, U44, U46, U48, U50, U52, U54, U56, U58, U60, U62, U64, U66, U68, U70, U72, U74, U76, U78, U80: 4MB Flash; SO08

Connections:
3.3V: C1.1, C2.1, C3.1, D1.A, D4.A, J1.2, J2.VCC, J4.2, J5.2, J8.2, JP1.2, JP4.2, R3.2, R4.2, U1.14, U1.17, U3.3, U3.7, U3.8
3.3V1: C4.1, C5.1, C6.1, D3.A, D6.A, J6.2, J7.2, J10.VCC, J11.2, J12.2, JP5.2, JP6.2, R5.2, R6.2, U2.14, U2.17, U4.3, U4.7, U4.8
3.3V2: C7.1, C8.1, C9.1, D7.A, D9.A, J13.2, J14.2, J16.VCC, J17.2, J18.2, JP8.2, JP9.2, R9.2, R10.2, U5.14, U5.17, U6.3, U6.7, U6.8
3.3V3: C10.1, C11.1, C12.1, D10.A, D12.A, J19.2, J20.2, J22.VCC, J23.2, J24.2, JP11.2, JP12.2, R15.2, R16.2, U7.14, U7.17, U8.3, U8.7, U8.8
3.3V4: C13.1, C14.1, C15.1, D13.A, D15.A, J25.2, J26.2, J28.VCC, J29.2, J30.2, JP14.2, JP15.2, R19.2, R20.2, U9.14, U9.17, U10.3, U10.7, U10.8
3.3V5: C16.1, C17.1, C18.1, D16.A, D18.A, J31.2, J32.2, J34.VCC, J35.2, J36.2, JP17.2, JP18.2, R23.2, R24.2, U11.14, U11.17, U12.3, U12.7, U12.8
3.3V6: C19.1, C20.1, C21.1, D19.A, D21.A, J37.2, J38.2, J40.VCC, J41.2, J42.2, JP20.2, JP21.2, R27.2, R28.2, U13.14, U13.17, U14.3, U14.7, U14.8
3.3V7: C22.1, C23.1, C24.1, D22.A, D24.A, J43.2, J44.2, J46.VCC, J47.2, J48.2, JP23.2, JP24.2, R31.2, R32.2, U15.14, U15.17, U16.3, U16.7, U16.8
3.3V8: C25.1, C26.1, C27.1, D25.A, D27.A, J49.2, J50.2, J52.VCC, J53.2, J54.2, JP26.2, JP27.2, R35.2, R36.2, U17.14, U17.17, U18.3, U18.7, U18.8
3.3V9: C28.1, C29.1, C30.1, D28.A, D30.A, J55.2, J56.2, J58.VCC, J59.2, J60.2, JP29.2, JP30.2, R39.2, R40.2, U19.14, U19.17, U20.3, U20.7, U20.8
3.3V10: C31.1, C32.1, C33.1, D31.A, D33.A, J61.2, J62.2, J64.VCC, J65.2, J66.2, JP32.2, JP33.2, R43.2, R44.2, U21.14, U21.17, U22.3, U22.7, U22.8
3.3V11: C34.1, C35.1, C36.1, D34.A, D36.A, J67.2, J68.2, J70.VCC, J71.2, J72.2, JP35.2, JP36.2, R47.2, R48.2, U23.14, U23.17, U24.3, U24.7, U24.8
3.3V12: C37.1, C38.1, C39.1, D37.A, D39.A, J73.2, J74.2, J76.VCC, J77.2, J78.2, JP38.2, JP39.2, R51.2, R52.2, U25.14, U25.17, U26.3, U26.7, U26.8
3.3V13: C40.1, C41.1, C42.1, D40.A, D42.A, J79.2, J80.2, J82.VCC, J83.2, J84.2, JP41.2, JP42.2, R55.2, R56.2, U27.14, U27.17, U28.3, U28.7, U28.8
3.3V14: C43.1, C44.1, C45.1, D43.A, D45.A, J85.2, J86.2, J88.VCC, J89.2, J90.2, JP44.2, JP45.2, R59.2, R60.2, U29.14, U29.17, U30.3, U30.7, U30.8
3.3V15: C46.1, C47.1, C48.1, D46.A, D48.A, J91.2, J92.2, J94.VCC, J95.2, J96.2, JP47.2, JP48.2, R63.2, R64.2, U31.14, U31.17, U32.3, U32.7, U32.8
3.3V16: C49.1, C50.1, C51.1, D49.A, D51.A, J97.2, J98.2, J100.VCC, J101.2, J102.2, JP50.2, JP51.2, R67.2, R68.2, U33.14, U33.17, U34.3, U34.7, U34.8
3.3V17: C52.1, C53.1, C54.1, D52.A, D54.A, J103.2, J104.2, J106.VCC, J107.2, J108.2, JP53.2, JP54.2, R71.2, R72.2, U35.14, U35.17, U36.3, U36.7, U36.8
3.3V18: C55.1, C56.1, C57.1, D55.A, D57.A, J109.2, J110.2, J112.VCC, J113.2, J114.2, JP56.2, JP57.2, R75.2, R76.2, U37.14, U37.17, U38.3, U38.7, U38.8
3.3V19: C58.1, C59.1, C60.1, D58.A, D60.A, J115.2, J116.2, J118.VCC, J119.2, J120.2, JP59.2, JP60.2, R79.2, R80.2, U39.14, U39.17, U40.3, U40.7, U40.8
3.3V20: C61.1, C62.1, C63.1, D61.A, D63.A, J121.2, J122.2, J124.VCC, J125.2, J126.2, JP62.2, JP63.2, R83.2, R84.2, U41.14, U41.17, U42.3, U42.7, U42.8
3.3V21: C64.1, C65.1, C66.1, D64.A, D66.A, J127.2, J128.2, J130.VCC, J131.2, J132.2, JP65.2, JP66.2, R87.2, R88.2, U43.14, U43.17, U44.3, U44.7, U44.8
3.3V22: C67.1, C68.1, C69.1, D67.A, D69.A, J133.2, J134.2, J136.VCC, J137.2, J138.2, JP68.2, JP69.2, R91.2, R92.2, U45.14, U45.17, U46.3, U46.7, U46.8
3.3V23: C70.1, C71.1, C72.1, D70.A, D72.A, J139.2, J140.2, J142.VCC, J143.2, J144.2, JP71.2, JP72.2, R95.2, R96.2, U47.14, U47.17, U48.3, U48.7, U48.8
3.3V24: C73.1, C74.1, C75.1, D73.A, D75.A, J145.2, J146.2, J148.VCC, J149.2, J150.2, JP74.2, JP75.2, R99.2, R100.2, U49.14, U49.17, U50.3, U50.7, U50.8
3.3V25: C76.1, C77.1, C78.1, D76.A, D78.A, J151.2, J152.2, J154.VCC, J155.2, J156.2, JP77.2, JP78.2, R103.2, R104.2, U51.14, U51.17, U52.3, U52.7, U52.8
3.3V26: C79.1, C80.1, C81.1, D79.A, D81.A, J157.2, J158.2, J160.VCC, J161.2, J162.2, JP80.2, JP81.2, R107.2, R108.2, U53.14, U53.17, U54.3, U54.7, U54.8
3.3V27: C82.1, C83.1, C84.1, D82.A, D84.A, J163.2, J164.2, J166.VCC, J167.2, J168.2, JP83.2, JP84.2, R111.2, R112.2, U55.14, U55.17, U56.3, U56.7, U56.8
3.3V28: C85.1, C86.1, C87.1, D85.A, D87.A, J169.2, J170.2, J172.VCC, J173.2, J174.2, JP86.2, JP87.2, R115.2, R116.2, U57.14, U57.17, U58.3, U58.7, U58.8
3.3V29: C88.1, C89.1, C90.1, D88.A, D90.A, J175.2, J176.2, J178.VCC, J179.2, J180.2, JP89.2, JP90.2, R119.2, R120.2, U59.14, U59.17, U60.3, U60.7, U60.8
3.3V30: C91.1, C92.1, C93.1, D91.A, D93.A, J181.2, J182.2, J184.VCC, J185.2, J186.2, JP92.2, JP93.2, R123.2, R124.2, U61.14, U61.17, U62.3, U62.7, U62.8
3.3V31: C94.1, C95.1, C96.1, D94.A, D96.A, J187.2, J188.2, J190.VCC, J191.2, J192.2, JP95.2, JP96.2, R127.2, R128.2, U63.14, U63.17, U64.3, U64.7, U64.8
3.3V32: C97.1, C98.1, C99.1, D97.A, D99.A, J193.2, J194.2, J196.VCC, J197.2, J198.2, JP98.2, JP99.2, R131.2, R132.2, U65.14, U65.17, U66.3, U66.7, U66.8
3.3V33: C100.1, C101.1, C102.1, D100.A, D102.A, J199.2, J200.2, J202.VCC, J203.2, J204.2, JP101.2, JP102.2, R135.2, R136.2, U67.14, U67.17, U68.3, U68.7, U68.8
3.3V34: C103.1, C104.1, C105.1, D103.A, D105.A, J205.2, J206.2, J208.VCC, J209.2, J210.2, JP104.2, JP105.2, R139.2, R140.2, U69.14, U69.17, U70.3, U70.7, U70.8
3.3V35: C106.1, C107.1, C108.1, D106.A, D108.A, J211.2, J212.2, J214.VCC, J215.2, J216.2, JP107.2, JP108.2, R143.2, R144.2, U71.14, U71.17, U72.3, U72.7, U72.8
3.3V36: C109.1, C110.1, C111.1, D109.A, D111.A, J217.2, J218.2, J220.VCC, J221.2, J222.2, JP110.2, JP111.2, R147.2, R148.2, U73.14, U73.17, U74.3, U74.7, U74.8
3.3V37: C112.1, C113.1, C114.1, D112.A, D114.A, J223.2, J224.2, J226.VCC, J227.2, J228.2, JP113.2, JP114.2, R151.2, R152.2, U75.14, U75.17, U76.3, U76.7, U76.8
3.3V38: C115.1, C116.1, C117.1, D115.A, D117.A, J229.2, J230.2, J232.VCC, J233.2, J234.2, JP116.2, JP117.2, R155.2, R156.2, U77.14, U77.17, U78.3, U78.7, U78.8
3.3V39: C118.1, C119.1, C120.1, D118.A, D120.A, J235.2, J236.2, J238.VCC, J239.2, J240.2, JP119.2, JP120.2, R159.2, R160.2, U79.14, U79.17, U80.3, U80.7, U80.8
!CS_EE: J5.5, U1.6, U3.1
!CS_EE1: J12.5, U2.6, U4.1
!CS_EE2: J18.5, U5.6, U6.1
!CS_EE3: J24.5, U7.6, U8.1
!CS_EE4: J30.5, U9.6, U10.1
!CS_EE5: J36.5, U11.6, U12.1
!CS_EE6: J42.5, U13.6, U14.1
!CS_EE7: J48.5, U15.6, U16.1
!CS_EE8: J54.5, U17.6, U18.1
!CS_EE9: J60.5, U19.6, U20.1
!CS_EE10: J66.5, U21.6, U22.1
!CS_EE11: J72.5, U23.6, U24.1
!CS_EE12: J78.5, U25.6, U26.1
!CS_EE13: J84.5, U27.6, U28.1
!CS_EE14: J90.5, U29.6, U30.1
!CS_EE15: J96.5, U31.6, U32.1
!CS_EE16: J102.5, U33.6, U34.1
!CS_EE17: J108.5, U35.6, U36.1
!CS_EE18: J114.5, U37.6, U38.1
!CS_EE19: J120.5, U39.6, U40.1
!CS_EE20: J126.5, U41.6, U42.1
!CS_EE21: J132.5, U43.6, U44.1
!CS_EE22: J138.5, U45.6, U46.1
!CS_EE23: J144.5, U47.6, U48.1
!CS_EE24: J150.5, U49.6, U50.1
!CS_EE25: J156.5, U51.6, U52.1
!CS_EE26: J162.5, U53.6, U54.1
!CS_EE27: J168.5, U55.6, U56.1
!CS_EE28: J174.5, U57.6, U58.1
!CS_EE29: J180.5, U59.6, U60.1
!CS_EE30: J186.5, U61.6, U62.1
!CS_EE31: J192.5, U63.6, U64.1
!CS_EE32: J198.5, U65.6, U66.1
!CS_EE33: J204.5, U67.6, U68.1
!CS_EE34: J210.5, U69.6, U70.1
!CS_EE35: J216.5, U71.6, U72.1
!CS_EE36: J222.5, U73.6, U74.1
!CS_EE37: J228.5, U75.6, U76.1
!CS_EE38: J234.5, U77.6, U78.1
!CS_EE39: J240.5, U79.6, U80.1
!INT: J3.1, U1.13
!INT1: J9.1, U2.13
!INT2: J15.1, U5.13
!INT3: J21.1, U7.13
!INT4: J27.1, U9.13
!INT5: J33.1, U11.13
!INT6: J39.1, U13.13
!INT7: J45.1, U15.13
!INT8: J51.1, U17.13
!INT9: J57.1, U19.13
!INT10: J63.1, U21.13
!INT11: J69.1, U23.13
!INT12: J75.1, U25.13
!INT13: J81.1, U27.13
!INT14: J87.1, U29.13
!INT15: J93.1, U31.13
!INT16: J99.1, U33.13
!INT17: J105.1, U35.13
!INT18: J111.1, U37.13
!INT19: J117.1, U39.13
!INT20: J123.1, U41.13
!INT21: J129.1, U43.13
!INT22: J135.1, U45.13
!INT23: J141.1, U47.13
!INT24: J147.1, U49.13
!INT25: J153.1, U51.13
!INT26: J159.1, U53.13
!INT27: J165.1, U55.13
!INT28: J171.1, U57.13
!INT29: J177.1, U59.13
!INT30: J183.1, U61.13
!INT31: J189.1, U63.13
!INT32: J195.1, U65.13
!INT33: J201.1, U67.13
!INT34: J207.1, U69.13
!INT35: J213.1, U71.13
!INT36: J219.1, U73.13
!INT37: J225.1, U75.13
!INT38: J231.1, U77.13
!INT39: J237.1, U79.13
!RST: J3.2, R4.1, U1.2
!RST1: J9.2, R6.1, U2.2
!RST2: J15.2, R10.1, U5.2
!RST3: J21.2, R16.1, U7.2
!RST4: J27.2, R20.1, U9.2
!RST5: J33.2, R24.1, U11.2
!RST6: J39.2, R28.1, U13.2
!RST7: J45.2, R32.1, U15.2
!RST8: J51.2, R36.1, U17.2
!RST9: J57.2, R40.1, U19.2
!RST10: J63.2, R44.1, U21.2
!RST11: J69.2, R48.1, U23.2
!RST12: J75.2, R52.1, U25.2
!RST13: J81.2, R56.1, U27.2
!RST14: J87.2, R60.1, U29.2
!RST15: J93.2, R64.1, U31.2
!RST16: J99.2, R68.1, U33.2
!RST17: J105.2, R72.1, U35.2
!RST18: J111.2, R76.1, U37.2
!RST19: J117.2, R80.1, U39.2
!RST20: J123.2, R84.1, U41.2
!RST21: J129.2, R88.1, U43.2
!RST22: J135.2, R92.1, U45.2
!RST23: J141.2, R96.1, U47.2
!RST24: J147.2, R100.1, U49.2
!RST25: J153.2, R104.1, U51.2
!RST26: J159.2, R108.1, U53.2
!RST27: J165.2, R112.1, U55.2
!RST28: J171.2, R116.1, U57.2
!RST29: J177.2, R120.1, U59.2
!RST30: J183.2, R124.1, U61.2
!RST31: J189.2, R128.1, U63.2
!RST32: J195.2, R132.1, U65.2
!RST33: J201.2, R136.1, U67.2
!RST34: J207.2, R140.1, U69.2
!RST35: J213.2, R144.1, U71.2
!RST36: J219.2, R148.1, U73.2
!RST37: J225.2, R152.1, U75.2
!RST38: J231.2, R156.1, U77.2
!RST39: J237.2, R160.1, U79.2
GND: C1.2, C2.2, C3.2, J1.1, J2.GND, J4.1, J5.6, J8.1, JP2.1, U1.16, U3.4
GND1: C4.2, C5.2, C6.2, J6.1, J7.1, J10.GND, J11.1, J12.6, JP3.1, U2.16, U4.4
GND2: C7.2, C8.2, C9.2, J13.1, J14.1, J16.GND, J17.1, J18.6, JP7.1, U5.16, U6.4
GND3: C10.2, C11.2, C12.2, J19.1, J20.1, J22.GND, J23.1, J24.6, JP10.1, U7.16, U8.4
GND4: C13.2, C14.2, C15.2, J25.1, J26.1, J28.GND, J29.1, J30.6, JP13.1, U9.16, U10.4
GND5: C16.2, C17.2, C18.2, J31.1, J32.1, J34.GND, J35.1, J36.6, JP16.1, U11.16, U12.4
GND6: C19.2, C20.2, C21.2, J37.1, J38.1, J40.GND, J41.1, J42.6, JP19.1, U13.16, U14.4
GND7: C22.2, C23.2, C24.2, J43.1, J44.1, J46.GND, J47.1, J48.6, JP22.1, U15.16, U16.4
GND8: C25.2, C26.2, C27.2, J49.1, J50.1, J52.GND, J53.1, J54.6, JP25.1, U17.16, U18.4
GND9: C28.2, C29.2, C30.2, J55.1, J56.1, J58.GND, J59.1, J60.6, JP28.1, U19.16, U20.4
GND10: C31.2, C32.2, C33.2, J61.1, J62.1, J64.GND, J65.1, J66.6, JP31.1, U21.16, U22.4
GND11: C34.2, C35.2, C36.2, J67.1, J68.1, J70.GND, J71.1, J72.6, JP34.1, U23.16, U24.4
GND12: C37.2, C38.2, C39.2, J73.1, J74.1, J76.GND, J77.1, J78.6, JP37.1, U25.16, U26.4
GND13: C40.2, C41.2, C42.2, J79.1, J80.1, J82.GND, J83.1, J84.6, JP40.1, U27.16, U28.4
GND14: C43.2, C44.2, C45.2, J85.1, J86.1, J88.GND, J89.1, J90.6, JP43.1, U29.16, U30.4
GND15: C46.2, C47.2, C48.2, J91.1, J92.1, J94.GND, J95.1, J96.6, JP46.1, U31.16, U32.4
GND16: C49.2, C50.2, C51.2, J97.1, J98.1, J100.GND, J101.1, J102.6, JP49.1, U33.16, U34.4
GND17: C52.2, C53.2, C54.2, J103.1, J104.1, J106.GND, J107.1, J108.6, JP52.1, U35.16, U36.4
GND18: C55.2, C56.2, C57.2, J109.1, J110.1, J112.GND, J113.1, J114.6, JP55.1, U37.16, U38.4
GND19: C58.2, C59.2, C60.2, J115.1, J116.1, J118.GND, J119.1, J120.6, JP58.1, U39.16, U40.4
GND20: C61.2, C62.2, C63.2, J121.1, J122.1, J124.GND, J125.1, J126.6, JP61.1, U41.16, U42.4
GND21: C64.2, C65.2, C66.2, J127.1, J128.1, J130.GND, J131.1, J132.6, JP64.1, U43.16, U44.4
GND22: C67.2, C68.2, C69.2, J133.1, J134.1, J136.GND, J137.1, J138.6, JP67.1, U45.16, U46.4
GND23: C70.2, C71.2, C72.2, J139.1, J140.1, J142.GND, J143.1, J144.6, JP70.1, U47.16, U48.4
GND24: C73.2, C74.2, C75.2, J145.1, J146.1, J148.GND, J149.1, J150.6, JP73.1, U49.16, U50.4
GND25: C76.2, C77.2, C78.2, J151.1, J152.1, J154.GND, J155.1, J156.6, JP76.1, U51.16, U52.4
GND26: C79.2, C80.2, C81.2, J157.1, J158.1, J160.GND, J161.1, J162.6, JP79.1, U53.16, U54.4
GND27: C82.2, C83.2, C84.2, J163.1, J164.1, J166.GND, J167.1, J168.6, JP82.1, U55.16, U56.4
GND28: C85.2, C86.2, C87.2, J169.1, J170.1, J172.GND, J173.1, J174.6, JP85.1, U57.16, U58.4
GND29: C88.2, C89.2, C90.2, J175.1, J176.1, J178.GND, J179.1, J180.6, JP88.1, U59.16, U60.4
GND30: C91.2, C92.2, C93.2, J181.1, J182.1, J184.GND, J185.1, J186.6, JP91.1, U61.16, U62.4
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

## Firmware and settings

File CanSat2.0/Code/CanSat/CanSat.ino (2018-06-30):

/*
  CanSat GOSA
  Code for a tiny probe to investigate existance of life
  Copyright (C) 2018  Jakub Suchánek, suchanek989@seznam.cz
  http://github.com/suchanekj/CanSatGOSA

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
  Licence can be viewed at
  https://github.com/suchanekj/CanSatGOSA/blob/master/LICENSE

  Please maintain this license information along with authorship
  and copyright notices in any redistribution of this code
  **********************************************************************************
*/

#include <USBAPI.h>
#include <Wire.h>
#include <EEPROM.h>
#include <avr/wdt.h>
#include <SD.h>
#include <SPI.h>
#include "_CanSat.h"

#if defined(BAROMETER) || defined(RANGING_SENSOR) || defined(COMPASS) || defined(HUMIDITYSENSOR) || defined(COMPASS2) || defined(LIGHT_SENSOR)
TwoWire *i2c;
#endif

#ifdef BAROMETER
BMP180 bmp;
long int alt_mod;
#endif

#ifdef HUMIDITY_SENSOR
Adafruit_Si7021 hum = Adafruit_Si7021();
#endif

#ifdef RANGING_SENSOR
VL53L0X ranging_sensor;
#endif

#ifdef COMPASS
LSM303AGR_ACC_Sensor *Acc;
LSM303AGR_MAG_Sensor *Mag;
#endif

#ifdef COMPASS2
Adafruit_HMC5883_Unified mag = Adafruit_HMC5883_Unified(12345);
#endif

#ifdef LIGHT_SENSOR
Adafruit_TSL2591 tsl = Adafruit_TSL2591(2591);
#endif

#ifdef UV_SENSOR
Adafruit_VEML6070 uv = Adafruit_VEML6070();
#endif

#ifdef SPECTROSCOP
AS726X spectroscop;
#endif

void changeInitState(int new_state) {
    EEPROM.put(EEPROM_CURRENT_MODULE, new_state);
    init_state = new_state;
}

long old_bar_time;
long old_bar_alt;

ISR(WDT_vect) {
}

void setup() {

    flight_state = EEPROM.read(EEPROM_STATE);
    if(STATES_N <= flight_state) flight_state = INIT;
    EEPROM.put(EEPROM_STATE, (byte) INIT);
    init_state = 0;
    if(flight_state != BOOTING) changeState(INIT);

    if (flight_state == INIT) {
        EEPROM.put(EEPROM_MODULES_0, (byte) 0);
        EEPROM.put(EEPROM_MODULES_1, (byte) 0);
        EEPROM.put(EEPROM_GPS, (byte) 0);
        EEPROM.put(EEPROM_CURRENT_MODULE, (byte) 0);
        barometer_on = 1;
        radio_on = 1;
        humidity_sensor_on = 1;
        ranging_sensor_on = 1;
        compass_on = 1;
        gsm_on = 1;
        gps_on = 1;
        light_sensor_on = 1;
        uv_sensor_on = 1;
        sd_on = 1;
        compass2_on = 1;
        i2c_on = 1;
    } else {
        if(flight_state == INIT || flight_state == BOOTING) {
            byte old_init_state = EEPROM.read(EEPROM_CURRENT_MODULE);
            if (old_init_state != INIT_DONE && old_init_state != 0) {
                uint16_t working_modules = (EEPROM.read(EEPROM_MODULES_0) << 8) + EEPROM.read(EEPROM_MODULES_1);
#ifdef GPS
                if(old_init_state == GPS) {
                    byte GPS_counter = EEPROM.read(EEPROM_GPS);
                    if(GPS_counter < 2) {
                        EEPROM.put(EEPROM_GPS, (byte)(GPS_counter + (byte) 1));
                    }
                    else {
                        working_modules |= 1 << GPS;
                    }
                }
                else working_modules |= 1 << old_init_state;
#endif
#ifndef GPS
                working_modules |= 1 << old_init_state;
#endif
                EEPROM.put(EEPROM_MODULES_0, (byte)(working_modules >> 8));
                EEPROM.put(EEPROM_MODULES_1, (byte)working_modules);
            }
        }
        uint16_t working_modules = (EEPROM.read(EEPROM_MODULES_0) << 8) + EEPROM.read(EEPROM_MODULES_1);
#ifdef DEBUG
        DEBUG_SERIAL.begin(9600);
        while (!DEBUG_SERIAL);
        DEBUG_SERIAL.print("broken modules are ");
        DEBUG_SERIAL.println(flight_state, BIN);
#endif
#ifdef BAROMETER
        barometer_on = 1 - (working_modules >> BAROMETER) & 1;
#endif
#ifdef RADIO
        radio_on = 1 - (working_modules >> RADIO) & 1;
#endif
#ifdef HUMIDITY_SENSOR
        humidity_sensor_on = 1 - (working_modules >> HUMIDITY_SENSOR) & 1;
#endif
#ifdef RANGING_SENSOR
        ranging_sensor_on = 1 - (working_modules >> RANGING_SENSOR) & 1;
#endif
#ifdef COMPASS
        compass_on = 1 - (working_modules >> COMPASS) & 1;
#endif
#ifdef GSM
        gsm_on = 1 - (working_modules >> GSM) & 1;
#endif
#ifdef GPS
        gps_on = 1 - (working_modules >> GPS) & 1;
#endif
#ifdef LIGHT_SENSOR
        light_sensor_on = 1 - (working_modules >> LIGHT_SENSOR) & 1;
#endif
#ifdef UV_SENSOR
        uv_sensor_on = 1 - (working_modules >> UV_SENSOR) & 1;
#endif
#ifdef SD
        sd_on = 1 - (working_modules >> SD) & 1;
#endif
#ifdef COMPASS2
        compass2_on = 1 - (working_modules >> COMPASS2) & 1;
#endif
        if (flight_state == OPENING_ARMS || flight_state == BREAKING || flight_state == FLYING ||
            flight_state == LANDING) {
            changeState(PARACHUTING);
        }
    }

    //PWM output to Flight Controller

    wdt_enable(WDTO_4S);
    wdt_reset();

    pinMode(FC_PWM_1, OUTPUT);
    pinMode(FC_PWM_2, OUTPUT);
    pinMode(FC_PWM_3, OUTPUT);
    pinMode(FC_PWM_4, OUTPUT);
    pinMode(FC_PWM_5, OUTPUT);
    pinMode(FC_PWM_6, OUTPUT);
    pinMode(FC_PWM_7, OUTPUT);
    pinMode(FC_PWM_8, OUTPUT);

    //LEDs

    for (int i = 0; i < 4; i++) {
        pinMode(LED[i], OUTPUT);
    }


    //GSM module

//    pinMode(GSM_SLEEP, OUTPUT);
//    pinMode(GSM_POWER_KEY, OUTPUT);

    //GPS module

//    GPS_SERIAL.begin(9600);

    //Servo

    pinMode(SERVO_PARACHUTE, OUTPUT);
    servo_parachute.attach(SERVO_PARACHUTE);

    if (flight_state == PARACHUTING) servo_parachute.write(SERVO_PARACUTE_OPEN);
    else
        servo_parachute.write(SERVO_PARACUTE_CLOSED);

    pinMode(SERVO_SAMPLE, OUTPUT);
    servo_sample.attach(SERVO_SAMPLE);
    servo_sample.write(0);

    //O2 sensor

    pinMode(O2, INPUT);

    //CO2 sensor

    pinMode(CO2, INPUT);

    //Camera power

    digitalWrite(CAMERA_POWER, LOW);
    pinMode(CAMERA_POWER, OUTPUT);

    //Flight Controller power

    digitalWrite(FC_POWER, LOW);
    pinMode(FC_POWER, OUTPUT);

    //Radio transmitter

    pinMode(RFM_INT, INPUT);
    digitalWrite(RFM_SS, HIGH);
    pinMode(RFM_SS, OUTPUT);

    //SD card

    digitalWrite(SD_SS, HIGH);
    pinMode(SD_SS, OUTPUT);

    //Read battery voltage

    pinMode(BATTERY_VOLTAGE, INPUT);

    pinMode(O2, INPUT);
    pinMode(CO2, INPUT);
    pinMode(O3, INPUT);

#ifdef DEBUG
    // Led blinking.
    if (flight_state == INIT) {
        for (int i = 0; i < 20; i++) {
            for (int j = 0; j < 4; j++) digitalWrite(LED[j], HIGH);
            delay(250);
            for (int j = 0; j < 4; j++) digitalWrite(LED[j], LOW);
            delay(250);
            wdt_reset();
        }
    }
    DEBUG_SERIAL.begin(9600);
    DEBUG_SERIAL.print("REBOOT at ");
    DEBUG_SERIAL.println(flight_state);
#endif

    if(flight_state == INIT)
        changeState(BOOTING);

#if defined(BAROMETER) || defined(RANGING_SENSOR) || defined(COMPASS) || defined(HUMIDITY_SENSOR) || defined(COMPASS2) || defined(LIGHT_SENSOR)
// Initialize I2C bus.
    if(i2c_on) {
        changeInitState(I2C);
        i2c = new TwoWire();
        i2c->begin();
        wdt_reset();
#ifdef DEBUG
        DEBUG_SERIAL.println("I2C initialized");
#endif
    }
#endif

#ifdef BAROMETER
    if (barometer_on && i2c_on) {
        if (bmp.begin())
            DEBUG_SERIAL.println("BMP180 init success");
        else
        {
            //In case of error let user know of the problem
            DEBUG_SERIAL.println("BMP180 init fail (disconnected?)\n\n");
            while(1); // Pause forever.
        }
        wdt_reset();


        double T,P;

        // Get a new pressure reading:

        if(flight_state == BOOTING || flight_state == INIT) {
            delay(1000);
            bmp.getData(T,P);
            wdt_reset();
            delay(1000);
            bmp.getData(T,P);
            delay(1000);
            bmp.getData(T,P);
            wdt_reset();
        }
        else
            bmp.getData(T,P);

        while(P < 1000 || P > 1200) bmp.getData(T,P);

        bar_alt = (long)(((double)1013.25 - P) * (double)900.0);

        alt_mod = (long)STARTING_ALT - (long)bar_alt;

        bar_alt_0 = bar_alt;

        old_bar_time = -10000;

        wdt_reset();

        DEBUG_SERIAL.println(bar_alt);
        DEBUG_SERIAL.println(alt_mod);
#ifdef DEBUG
        DEBUG_SERIAL.println("barometer initialized");
#endif
    }
#endif

#ifdef HUMIDITY_SENSOR
    if(humidity_sensor_on && i2c_on) {
        changeInitState(HUMIDITY_SENSOR);
        if (!hum.begin()) {
#ifdef DEBUG
            DEBUG_SERIAL.println("Did not find Si7021 sensor!");
#endif
            while (true);
        }
#ifdef DEBUG
        DEBUG_SERIAL.println("humidity initialized");
#endif
    }

#endif

#ifdef RANGING_SENSOR
    if (ranging_sensor_on) {
        changeInitState(RANGING_SENSOR);
        ranging_sensor.init();
        ranging_sensor.setTimeout(300);

        // Start continuous back-to-back mode (take readings as
        // fast as possible).  To use continuous timed mode
        // instead, provide a desired inter-measurement period in
        // ms (e.g. sensor.startContinuous(100)).
        ranging_sensor.startContinuous();
        wdt_reset();
#ifdef DEBUG
        DEBUG_SERIAL.println("ranging initialized");
#endif
    }
#endif

#ifdef COMPASS
    if(compass_on) {
        changeInitState(COMPASS);
        Acc = new LSM303AGR_ACC_Sensor(i2c);
        wdt_reset();
#ifdef DEBUG
        DEBUG_SERIAL.println("Accelerometer initialized");
#endif
        Acc->Enable();
#ifdef DEBUG
        DEBUG_SERIAL.println("Accelerometer enabled");
#endif
        Mag = new LSM303AGR_MAG_Sensor(i2c);
#ifdef DEBUG
        DEBUG_SERIAL.println("Magnetometer initialized");
#endif
        Mag->Enable();
#ifdef DEBUG
        DEBUG_SERIAL.println("Magnetometer enabled");
#endif
    }
#endif

#ifdef GPS
    if (gps_on) {
        changeInitState(GPS);
        wdt_reset();
        GPS_init();
        wdt_reset();
#ifdef DEBUG
        DEBUG_SERIAL.println("GPS initialized");
#endif
    }
#endif


#ifdef RADIO
    if (radio_on) {
        changeInitState(RADIO);
        //Initialize radio
        radio.setCS(RFM_SS);
        radio.initialize(FREQUENCY, NODEID, NETWORKID);
        radio.setHighPower(); //To use the high power capabilities of the RFM69HW
        radio.encrypt(ENCRYPTKEY);
        radio.setFrequency(868000000);
        radio.setPowerLevel(28);
#ifdef DEBUG
        DEBUG_SERIAL.print("Transmitting at ");
        uint32_t f = radio.getFrequency();
        DEBUG_SERIAL.println(f);
#endif
    }
#endif

#ifdef COMPASS2
    if(compass2_on) {
        if (!mag.begin()) {
            /* There was a problem detecting the HMC5883 ... check your connections */
#ifdef DEBUG
            DEBUG_SERIAL.println("Ooops, no HMC5883 detected ... Check your wiring!");
#endif
            while (1);
        }
#ifdef DEBUG
        DEBUG_SERIAL.println("compass2 initialized");
#endif
    }
#endif

#ifdef LIGHT_SENSOR
    if(light_sensor_on && i2c_on) {
        // You can change the gain on the fly, to adapt to brighter/dimmer light situations
        //tsl.setGain(TSL2591_GAIN_LOW);    // 1x gain (bright light)
        tsl.setGain(TSL2591_GAIN_MED);      // 25x gain
        //tsl.setGain(TSL2591_GAIN_HIGH);   // 428x gain

        // Changing the integration time gives you a longer time over which to sense light
        // longer timelines are slower, but are good in very low light situtations!
        //tsl.setTiming(TSL2591_INTEGRATIONTIME_100MS);  // shortest integration time (bright light)
        // tsl.setTiming(TSL2591_INTEGRATIONTIME_200MS);
        tsl.setTiming(TSL2591_INTEGRATIONTIME_300MS);
        // tsl.setTiming(TSL2591_INTEGRATIONTIME_400MS);
        // tsl.setTiming(TSL2591_INTEGRATIONTIME_500MS);
        // tsl.setTiming(TSL2591_INTEGRATIONTIME_600MS);  // longest integration time (dim light)

#ifdef DEBUG
        /* Display the gain and integration time for reference sake */
        DEBUG_SERIAL.println(F("------------------------------------"));
        DEBUG_SERIAL.print(F("Gain:         "));
        tsl2591Gain_t gain = tsl.getGain();
        switch (gain) {
            case TSL2591_GAIN_LOW:
                DEBUG_SERIAL.println(F("1x (Low)"));
                break;
            case TSL2591_GAIN_MED:
                DEBUG_SERIAL.println(F("25x (Medium)"));
                break;
            case TSL2591_GAIN_HIGH:
                DEBUG_SERIAL.println(F("428x (High)"));
                break;
            case TSL2591_GAIN_MAX:
                DEBUG_SERIAL.println(F("9876x (Max)"));
                break;
        }
        DEBUG_SERIAL.print(F("Timing:       "));
        DEBUG_SERIAL.print((tsl.getTiming() + 1) * 100, DEC);
        DEBUG_SERIAL.println(F(" ms"));
        DEBUG_SERIAL.println(F("------------------------------------"));
        DEBUG_SERIAL.println(F(""));
#endif
    }
#endif

#ifdef UV_SENSOR
    if(uv_sensor_on && i2c_on) {
#ifdef DEBUG
        DEBUG_SERIAL.println("VEML6070 Test");
#endif
        uv.begin(VEML6070_1_T);
    }
#endif

#ifdef SD_CARD
    if(SD_on) {
        if (!SD.begin(SD_SS)) {
            DEBUG_SERIAL.println("Card failed, or not present");
            // don't do anything more:
            while(1);
        }
        DEBUG_SERIAL.println("SD initialized");
    }
#endif

#ifdef SPECTROSCOP
    if(spectroscop_on){
        spectroscop.begin();
    }
#endif

#ifdef LIGHT_SENSOR
    if(light_sensor_on && i2c_on) {
        if (tsl.begin())
        {
            DEBUG_SERIAL.println(F("Found a TSL2591 sensor"));
        }
        else
        {
            DEBUG_SERIAL.println(F("No sensor found ... check your wiring?"));
            while (1);
        }

        tsl.setGain(TSL2591_GAIN_MED);      // 25x gain
        //tsl.setGain(TSL2591_GAIN_HIGH);   // 428x gain

        // Changing the integration time gives you a longer time over which to sense light
        // longer timelines are slower, but are good in very low light situtations!
        //tsl.setTiming(TSL2591_INTEGRATIONTIME_100MS);  // shortest integration time (bright light)
        // tsl.setTiming(TSL2591_INTEGRATIONTIME_200MS);
        tsl.setTiming(TSL2591_INTEGRATIONTIME_300MS);
    }
#endif

//    flight_state = TESTING;
    changeInitState(INIT_DONE);
    wdt_reset();
//    drone_init();
    wdt_reset();
    transmitting_init();
    wdt_reset();
    send_init();
    wdt_reset();
    last_time_sent = 0;
    for (int j = 0; j < 4; j++) digitalWrite(LED[j], HIGH);
}

void loop() {
//    changeState(LANDED);
    wdt_reset();
#ifdef BAROMETER
    if(barometer_on && i2c_on) {
        changeInitState(BAROMETER);
        double T,P;

        bmp.getData(T,P);



        temperature = T * 100;
        if(P >= 1000 || P <= 1200) pressure = P * (double)100;

        bar_alt = (101325 - P * 100) * 9.0 + alt_mod;
        if(millis() - old_bar_time > 500) {
            bar_vel = (long)((old_bar_alt - bar_alt) * (long)1000) / (long)(millis() - old_bar_time);
            DEBUG_SERIAL.println((old_bar_alt - bar_alt) * 1000);
            DEBUG_SERIAL.println(millis() - old_bar_time);

            old_bar_time = millis();
            old_bar_alt = bar_alt;
        }
#ifdef DEBUGa
        DEBUG_SERIAL.print("Alt(cm): ");
        DEBUG_SERIAL.print(bar_alt);
    
        DEBUG_SERIAL.print("Pressure(Pa): ");
        DEBUG_SERIAL.print(pressure);
#endif
#ifdef DEBUGa
        DEBUG_SERIAL.print(" Temp: ");
        DEBUG_SERIAL.print(temperature);
        DEBUG_SERIAL.println();
#endif
    }
#endif
//
//    DEBUG_SERIAL.println("a");
//    delay(100);

#ifdef HUMIDITY_SENSOR
    if(humidity_sensor_on && i2c_on) {
        changeInitState(HUMIDITY_SENSOR);
        hum.readHumidity();
    }
#endif
//
//    DEBUG_SERIAL.println("a");
//    delay(100);

#ifdef RANGING_SENSOR
    if(ranging_sensor_on) {
        bottom_distance = ranging_sensor.readRangeContinuousMillimeters();
#ifdef DEBUG
        if (ranging_sensor.timeoutOccurred()) { DEBUG_SERIAL.println(" TIMEOUT"); }
#endif
    }
#endif

#ifdef COMPASS
    if(compass_on) {
        // Read accelerometer LSM303AGR.
        Acc->GetAxes(accelerometer);

        // Read magnetometer LSM303AGR.
        Mag->GetAxes(magnetometer);

        // Output data.
#if 0
        DEBUG_SERIAL.print("| Acc[mg]: ");
        DEBUG_SERIAL.print(accelerometer[0]);
        DEBUG_SERIAL.print(" ");
        DEBUG_SERIAL.print(accelerometer[1]);
        DEBUG_SERIAL.print(" ");
        DEBUG_SERIAL.print(accelerometer[2]);
        DEBUG_SERIAL.print(" | Mag[mGauss]: ");
        DEBUG_SERIAL.print(magnetometer[0]);
        DEBUG_SERIAL.print(" ");
        DEBUG_SERIAL.print(magnetometer[1]);
        DEBUG_SERIAL.print(" ");
        DEBUG_SERIAL.print(magnetometer[2]);
        DEBUG_SERIAL.println(" |");
#endif
    }
#endif

#ifdef GPS
    if(gps_on)
    {
        changeInitState(GPS);
        GPS_run();
    }
#endif

#ifdef COMPASS2
    if(compass2_on) {
        /* Get a new sensor event */
        sensors_event_t event;
        mag.getEvent(&event);
#ifdef DEBUG
        /* Display the results (magnetic vector values are in micro-Tesla (uT)) */
        DEBUG_SERIAL.print("X: "); DEBUG_SERIAL.print(event.magnetic.x); DEBUG_SERIAL.print("  ");
        DEBUG_SERIAL.print("Y: "); DEBUG_SERIAL.print(event.magnetic.y); DEBUG_SERIAL.print("  ");
        DEBUG_SERIAL.print("Z: "); DEBUG_SERIAL.print(event.magnetic.z); DEBUG_SERIAL.print("  ");DEBUG_SERIAL.println("uT");
#endif
        magnetometer[0] = event.magnetic.x + COMPASS_OFFSET_X;
        magnetometer[1] = event.magnetic.y + COMPASS_OFFSET_Y;
        magnetometer[2] = event.magnetic.z;

        heading = atan2(magnetometer[0], magnetometer[1]) + HEADING_OFFSET;
    }
#endif
//
//    DEBUG_SERIAL.println("a");
//    delay(100);

#ifdef LIGHT_SENSOR
    if(light_sensor_on && flight_state == LANDED && i2c_on) {
        changeInitState(LIGHT_SENSOR);
        uint32_t lum = tsl.getFullLuminosity();
        light_ir, light_vis;
        light_ir = lum >> 16;
        light_vis = lum & 0xFFFF;
    }
#endif
//
//    DEBUG_SERIAL.println("a");
//    delay(100);

#ifdef UV_SENSOR
    if(uv_sensor_on && i2c_on) {
        changeInitState(UV_SENSOR);
        uv_light = uv.readUV();
    }
#endif

//#ifdef DEBUG
//    DEBUG_SERIAL.println("a");
//    delay(100);
//#endif

#ifdef SPECTROSCOP
    spectroscop.takeMeasurements();
    spectroscopy[0] = spectroscop.getCalibratedR();
    spectroscopy[1] = spectroscop.getCalibratedS();
    spectroscopy[2] = spectroscop.getCalibratedT();
    spectroscopy[3] = spectroscop.getCalibratedU();
    spectroscopy[4] = spectroscop.getCalibratedV();
    spectroscopy[5] = spectroscop.getCalibratedW();
#endif

#ifdef COMPASS2
    if(!mag.begin())
    {
        /* There was a problem detecting the HMC5883 ... check your connections */
#ifdef DEBUG
        Serial.println("Ooops, no HMC5883 detected ... Check your wiring!");
#endif
        while(1);
    }
#endif

    o2 = analogRead(O2);
    co2 = analogRead(CO2) * 5 / 8.5;
    o3 = analogRead(O3);
    voltage = 2 * 5 * analogRead(BATTERY_VOLTAGE);
    if(/*my_fix.velocity_down > min(5000, 1000 + max(my_fix.altitude_cm() - DESTINATION_ALT, 0)) || */bar_vel > min(5000, 1000 + max(bar_alt - DESTINATION_ALT, 0)) || !barometer_on || voltage < 7000) changeState(PARACHUTING);
    runState();
    if(flight_state != PARACHUTING) servo_parachute.write(SERVO_PARACUTE_CLOSED);
    else servo_parachute.write(SERVO_PARACUTE_OPEN);
    //send_data();
}

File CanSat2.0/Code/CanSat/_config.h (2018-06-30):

/*
  CanSat GOSA
  Code for a tiny probe to investigate existance of life
  Copyright (C) 2018  Jakub Suchánek, suchanek989@seznam.cz
  http://github.com/suchanekj/CanSatGOSA

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
  Licence can be viewed at
  https://github.com/suchanekj/CanSatGOSA/blob/master/LICENSE

  Please maintain this license information along with authorship
  and copyright notices in any redistribution of this code
  **********************************************************************************
*/

#ifndef CANSAT_CONFIG_H
#define CANSAT_CONFIG_H

//#include "GPSport.h"
#include <Arduino.h>

/*
 ***********************************************************************************
 *  Landing spot
 */

#define STARTING_ALT 500
#define DESTINATION_LAT 499951500
#define DESTINATION_LON 145513150
#define DESTINATION_ALT 500

#define EARTH_RADIUS_M 6371009
#define RAD_PER_DEGREE (PI / 180.0)

/*
 ***********************************************************************************
 *  Subsystem definitions
 */
//comment any line to disable subsystem

#define DEBUG

#define BAROMETER 1
#define RADIO 2
#define HUMIDITY_SENSOR 3
//#define RANGING_SENSOR 4
//#define COMPASS 5
//#define GSM 6
//#define GPS 7
#define LIGHT_SENSOR 8
#define UV_SENSOR 9
#define SD_CARD 10
//#define COMPASS2 11
//#define SPECTROSCOP 12
#define I2C 13

#define INIT_DONE 14

/*
 ***********************************************************************************
 *  Parameter definitions
 */

//Radio Parameters

#define NODEID        2    //unique for each node on same network
#define NETWORKID     42  //the same on all nodes that talk to each other
#define GATEWAYID     1    //Receiving node
#define ENCRYPTKEY    "Suchy Na Mars!!!" //exactly the same 16 characters/bytes on all nodes!

//GSM parameters

#define GSM_WAIT_FOR_POWER_UP 10000

#define SERVO_PARACUTE_CLOSED (int)180
#define SERVO_PARACUTE_OPEN (int)0

#define EEPROM_STATE 0
#define EEPROM_MODULES_0 5
#define EEPROM_MODULES_1 9
#define EEPROM_GPS 14
#define EEPROM_CURRENT_MODULE 19

#define STATES_N 12

#define COMPASS_OFFSET_X 10.5
#define COMPASS_OFFSET_Y 32.5

#define HEADING_OFFSET 0

/*
 ***********************************************************************************
 *  Port definitions
 */

//debugging

#define DEBUG_SERIAL NeoSerial

//PWM output to Flight Controller


//#define FC_PWM_1 9
//#define FC_PWM_2 24
//#define FC_PWM_3 23
//#define FC_PWM_4 6
//#define FC_PWM_5 44
//#define FC_PWM_6 45
//#define FC_PWM_7 46
//#define FC_PWM_8 12

#define FC_PWM_1 12
#define FC_PWM_2 9
#define FC_PWM_3 23
#define FC_PWM_4 6
#define FC_PWM_5 45
#define FC_PWM_6 46
#define FC_PWM_7 24
#define FC_PWM_8 46

//Top board

const int LED[4] = {38, 85, 84, 83};

//GSM module

//#define GSM_SERIAL NeoSeial2
#define GSM_SLEEP 25
#define GSM_POWER_KEY 28

//GPS module


//Servo

#define SERVO_PARACHUTE 10
#define SERVO_SAMPLE 13

//O2 sensor

#define O2 A11
#define CO2 A12
#define O3 A13

//Camera power

#define CAMERA_POWER 26

//Flight Controller power

#define FC_POWER 27

//Radio transmitter

#define RFM_INT 2
#define RFM_SS 4

//SD card

#define SD_SS 57

//Read battery voltage

#define BATTERY_VOLTAGE A10

//Gamma read

#define GAMMA 3

#endif //CANSAT_CONFIG_H

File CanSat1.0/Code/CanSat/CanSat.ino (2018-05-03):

/*
  CanSat GOSA
  Code for a tiny probe to investigate existance of life
  Copyright (C) 2018  Jakub SuchĂˇnek, suchanek989@seznam.cz
  http://github.com/suchanekj/CanSatGOSA

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
  Licence can be viewed at
  https://github.com/suchanekj/CanSatGOSA/blob/master/LICENSE

  Please maintain this license information along with authorship
  and copyright notices in any redistribution of this code
  **********************************************************************************
*/

#include <USBAPI.h>
#include "CanSat.h"

#if defined(BAROMETER) || defined(RANGING_SENSOR) || defined(COMPASS) || defined(HUMIDITYSENSOR)
TwoWire *i2c;
#endif

#ifdef BAROMETER
MPL3115A2 barometer;
long int alt_mod;
#endif

#ifdef HUMIDITY_SENSOR
HIH7130 humidity;
#endif

#ifdef RANGING_SENSOR
VL53L0X ranging_sensor;
#endif

#ifdef COMPASS
LSM303AGR_ACC_Sensor *Acc;
LSM303AGR_MAG_Sensor *Mag;
#endif

void setup() {

    //PWM output to Flight Controller

    pinMode(FC_PWM_1, OUTPUT);
    pinMode(FC_PWM_2, OUTPUT);
    pinMode(FC_PWM_3, OUTPUT);
    pinMode(FC_PWM_4, OUTPUT);
    pinMode(FC_PWM_5, OUTPUT);
    pinMode(FC_PWM_6, OUTPUT);
    pinMode(FC_PWM_7, OUTPUT);
    pinMode(FC_PWM_8, OUTPUT);

    //Arms
//const int ARM_LED[4] = {47, 24, 76, 31};
//const int ARM_RANGING_XSHUT[4] = {38, 55, 11, 29};
//const int ARM_RANGING_INTERRUPT[4] = {19, 4, 53, 73};
    for (int i = 0; i < 4; i++) {
        pinMode(ARM_LED[i], OUTPUT);
        pinMode(ARM_RANGING_XSHUT[i], OUTPUT);
    }
    digitalWrite(ARM_RANGING_XSHUT[2], HIGH);
        pinMode(ARM_RANGING_INTERRUPT[2], INPUT);
    

    //Top board

    pinMode(TOP_LED, OUTPUT);

    //GSM module

    GSM_SERIAL.begin(9600);
    pinMode(GSM_SLEEP, OUTPUT);
    pinMode(GSM_POWER_KEY, OUTPUT);

    //GPS module

 //   GPS_SERIAL.begin(9600);

    //Servo

    pinMode(SERVO, OUTPUT);
    servo.attach(SERVO);

    //O2 sensor

    pinMode(O2, INPUT);

    //CO2 sensor

    pinMode(CO2, INPUT);

    //Camera power

    digitalWrite(CAMERA_POWER, HIGH);
    pinMode(CAMERA_POWER, OUTPUT);

    //Flight Controller power

    digitalWrite(FC_POWER, HIGH);
    pinMode(FC_POWER, OUTPUT);

    //Radio transmitter

    pinMode(RFM_INT, INPUT);
    pinMode(RFM_SS, OUTPUT);

    //Read battery voltage

    pinMode(BATTERY_VOLTAGE, INPUT);

    pinMode(A2, INPUT);
    pinMode(A4, INPUT);
    pinMode(A5, INPUT);
    pinMode(A6, INPUT);
    pinMode(A7, INPUT);
    pinMode(A8, INPUT);
    pinMode(A9, INPUT);
    pinMode(A10, INPUT);
    pinMode(A11, INPUT);
    pinMode(A12, INPUT);
    pinMode(A13, INPUT);
    pinMode(A14, INPUT);
    pinMode(A15, INPUT);

#ifdef DEBUG
    // Led blinking.
    for (int i = 0; i < 20; i++) {
        digitalWrite(TOP_LED, HIGH);
        delay(250);
        digitalWrite(TOP_LED, LOW);
        delay(250);
    }
    DEBUG_SERIAL.begin(9600);
    while(!DEBUG_SERIAL);
    DEBUG_SERIAL.println("REBOOT");
#endif



#if defined(BAROMETER) || defined(RANGING_SENSOR) || defined(COMPASS) || defined(HUMIDITYSENSOR)
// Initialize I2C bus.
    i2c = new TwoWire();
    i2c->begin();
#ifdef DEBUG
    Serial.println("I2C initialized");
#endif
#endif

#ifdef BAROMETER
    // Initlialize components.
    barometer.begin(); // Get sensor online

    barometer.setModeBarometer();
    barometer.setOversampleRate(7); // Set Oversample to the recommended 128
    barometer.enableEventFlags(); // Enable all three pressure and temp event flags 

    delay(1000);
    barometer.readPressure();
    delay(1000);
    barometer.readPressure();
    delay(1000);
    barometer.readPressure();

    bar_alt = (1013.25 - barometer.readPressure() / 100.0) * 900.0;

    alt_mod = STARTING_ALT - bar_alt;

    Serial.println(bar_alt);
    Serial.println(alt_mod);
#ifdef DEBUG
    Serial.println("barometer initialized");
#endif
#endif

#ifdef HUMIDITY_SENSOR
    // The address can be changed making the option of connecting multiple devices
    humidity.getAddr_HIH7130(HIH7130_DEFAULT_ADDRESS);   // 0x27
    humidity.begin();
    delay(500);
#endif

#ifdef RANGING_SENSOR
    ranging_sensor.init();
    ranging_sensor.setTimeout(300);

    // Start continuous back-to-back mode (take readings as
    // fast as possible).  To use continuous timed mode
    // instead, provide a desired inter-measurement period in
    // ms (e.g. sensor.startContinuous(100)).
    ranging_sensor.startContinuous();
#endif

#ifdef COMPASS
    Acc = new LSM303AGR_ACC_Sensor(i2c);
#ifdef DEBUG
    Serial.println("Accelerometer initialized");
#endif
    Acc->Enable();
#ifdef DEBUG
    Serial.println("Accelerometer enabled");
#endif
    Mag = new LSM303AGR_MAG_Sensor(i2c);
#ifdef DEBUG
    Serial.println("Magnetometer initialized");
#endif
    Mag->Enable();
#ifdef DEBUG
    Serial.println("Magnetometer enabled");
#endif
#endif

#ifdef GPS
    GPS_init();
#ifdef DEBUG
    Serial.println("GPS initialized");
    delay(1000);
#endif
#endif

    flight_state = PAR_WAIT;
    drone_init();
    transmitting_init(0, 0, 0);
    last_time_sent = 0;
    digitalWrite(TOP_LED, HIGH);
}

void loop() {
#ifdef BAROMETER
    
    pressure = barometer.readPressure() * 100.0;
    bar_alt = (101325 - pressure / 100.0) * 9.0 + alt_mod;
#ifdef DEBUGa
    Serial.print("Alt(cm): ");
    Serial.print(bar_alt);
    
    Serial.print("Pressure(Pa): ");
    Serial.print(pressure);
#endif

    temperature = barometer.readTemp() * 100;
#ifdef DEBUGa
    Serial.print(" Temp: ");
    Serial.print(temperature);
    Serial.println();
#endif
#endif

#ifdef HUMIDITY_SENSOR
    byte error;
    int8_t address;

    address = humidity.hih_i2cAddress;
    // The i2c_scanner uses the return value of
    // the Write.endTransmisstion to see if
    // a device did acknowledge to the address.
    Wire.beginTransmission(address);
    error = Wire.endTransmission();
    DEBUG_SERIAL.print(error);
    if (error == 0)
    {
        humidity.readRegister(address);

        Serial.println("Getting Readings from HIH7130");
        Serial.println(" ");
        // Read and print out the Relative Humidity, convert it to %RH
        humid = humidity.Measure_Humidity();

        // Read and print out the temperature, then convert to C and F scales
        temperature = humidity.Measure_Temperature();

        // Output data to screen
        Serial.print("Relative Humidity Reading: ");
        Serial.print(humid);
        Serial.println(" %RH");
        Serial.print("Temperature Reading in Celsius: ");
        Serial.print(temperature);
        Serial.println(" C");
        Serial.println("        ***************************        ");
        Serial.println(" ");
    }
    else
    {
        Serial.println("HIH7130 Disconnected!");
        Serial.println(" ");
        Serial.println("        ************        ");
        Serial.println(" ");
    }
#endif

#ifdef RANGING_SENSOR
    armDistance = ranging_sensor.readRangeContinuousMillimeters();
    if (ranging_sensor.timeoutOccurred()) { Serial.print(" TIMEOUT"); }

    Serial.println();
#endif
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

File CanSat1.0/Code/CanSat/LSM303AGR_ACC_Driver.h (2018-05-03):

/**
 ******************************************************************************
 * @file    LSM303AGR_ACC_driver.h
 * @author  MEMS Application Team
 * @version V1.1
 * @date    24-February-2016
 * @brief   LSM303AGR Accelerometer header driver file
 ******************************************************************************
 * @attention
 *
 * <h2><center>&copy; COPYRIGHT(c) 2017 STMicroelectronics</center></h2>
 *
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
 ******************************************************************************
 */

/* Define to prevent recursive inclusion -------------------------------------*/
#ifndef __LSM303AGR_ACC_DRIVER__H
#define __LSM303AGR_ACC_DRIVER__H

/* Includes ------------------------------------------------------------------*/
#include <stdint.h>

/* Exported types ------------------------------------------------------------*/

#ifdef __cplusplus
extern "C" {
#endif

//these could change accordingly with the architecture

#ifndef __ARCHDEP__TYPES
#define __ARCHDEP__TYPES

typedef unsigned char u8_t;
typedef unsigned short int u16_t;
typedef unsigned int u32_t;
typedef int i32_t;
typedef short int i16_t;
typedef signed char i8_t;

#endif /*__ARCHDEP__TYPES*/

/* Exported common structure --------------------------------------------------------*/

#ifndef __SHARED__TYPES
#define __SHARED__TYPES

typedef union{
	i16_t i16bit[3];
	u8_t u8bit[6];
} Type3Axis16bit_U;	

typedef union{
	i16_t i16bit;
	u8_t u8bit[2];
} Type1Axis16bit_U;

typedef union{
	i32_t i32bit;
	u8_t u8bit[4];
} Type1Axis32bit_U;

typedef enum {
  MEMS_SUCCESS = 0x01,
  MEMS_ERROR   = 0x00	
} mems_status_t;

#endif /*__SHARED__TYPES*/

/* Exported macro ------------------------------------------------------------*/

/* Exported constants --------------------------------------------------------*/

/************** I2C Address *****************/

#define LSM303AGR_ACC_I2C_ADDRESS         0x32

/************** Who am I  *******************/

#define LSM303AGR_ACC_WHO_AM_I         0x33

/* Private Function Prototype -------------------------------------------------------*/

void LSM303AGR_ACC_SwapHighLowByte(u8_t *bufferToSwap, u8_t numberOfByte, u8_t dimension);

/* Public Function Prototypes ------------------------------------------------*/

mems_status_t LSM303AGR_ACC_ReadReg( void *handle, u8_t Reg, u8_t* Data );
mems_status_t LSM303AGR_ACC_WriteReg( void *handle, u8_t Reg, u8_t Data );
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

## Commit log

2017-11-30 added basic circuit schematic
    [cansat.sch]
2017-12-28 Add first part of the model
    [Hull.ipt]
2017-12-31 Add drone parts model
    [Arm.0006.ipt, Arm.ipt, Batery_big.ipt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]
2018-01-04 Edit schematic
    [main.sch, top.sch]
2018-01-06 Edit schematic and model
    [Arm.0008.ipt, Arm_axel.0001.ipt, Arm_axel.ipt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]
2018-01-08 Edit schematic and footprints
    [main.sch, top.sch]
2018-01-16 Edit finish circuits and some model work
    [Arm.0006.ipt, Arm.0007.ipt, Arm.ipt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]
2018-01-16 Edit pcb and model
    [Battery_small.0001.ipt, Battery_small.ipt, CanSat.0002.iam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]
2018-01-17 Edit, add overall schematic, widen gaps in pcb
    [Circuit.ipt, Hull.ipt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]
2018-01-20 Edit power port distribution
    [Battery_small.ipt, CanSat.iam, Circuit.ipt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]
2018-02-02 Edit schematic and model, add images
    [Arm.0007.ipt, Arm.ipt, Battery_small.0001.ipt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]
2018-02-17 Add UV and Gamma detection, fix main pcb
    [arm-B.Cu.gbl, arm-B.Paste.gbp, arm-B.SilkS.gbo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]
2018-03-10 Edit arm conection in model
    [Hull.ipt, arm_stop.ipt]
2018-03-10 add new version of HULL
    [Arm_holder.ipt, Hull2.ipt]
2018-03-11 Add arm holders
    [deska.ipt, uchyt motoru-final.ipt, uchyt motoru.ipt]
2018-03-12 Add modular version of hull
    [Arm.ipt, Arm_axel.ipt, Arm_holder.ipt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]
2018-03-15 Fix arm holes in bottom hull
    [Arm.0008.ipt, Arm.ipt, Arm_axel.0001.ipt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]
2018-03-17 Add camera to assembly and reorganize scraper
    [Camera.ipt, CanSat.iam, Hull.ipt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]
2018-03-17 Edit model - finalizing the assembly, all components fit
    [CanSat.iam, Flight_controler.ipt, HGLRC Micro 13A 4in1 BLHeli_S.ipt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]
2018-03-17 Add servo holders in model
    [CanSat.iam, Hull.ipt, Hull_top.ipt]
2018-03-21 Add stabilization holders for flight controler
    [CanSat.iam, Hull.ipt, Motor_holder.ipt]
2018-04-01 Add base and libraries for final code
    [CanSat.iam]
2018-04-01 Add main schematic export
2018-04-01 add brackets to encapsulate data
2018-04-01 Add new schematic and pcb exports
2018-04-15 Edit arduino code
2018-04-17 Edit code - sensors functioning, add printable schematics
    [CanSat.ipn, cansat.sch, main.kicad_pcb]
2018-05-03 Add base for CanSat HATALOM 2.0
    [Arm.ipt, Battery.ipt, Camera.ipt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]
2018-05-07 Edite upper part of model
    [CanSat.iam, Circuit.ipt, Circuit_center.ipt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]
2018-05-10 Add new camera in model
    [Camera.ipt]
2018-05-25 Add three top boards and some other circuitry and modelling
    [CanSat.iam, Circuit.ipt, SIM808.ipt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]
2018-05-28 Add new pcbs - center and bottom - and fill the lower half of the model
    [Arm.ipt, Batt_pillar.ipt, Cam_SD_base.ipt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]
2018-06-03 Hull-component holders 1/2
    Cameras and gamma are not finished yet
    [CanSat.iam, Hull_batt_pillar.ipt, Hull_batt_pillar1.ipt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]
2018-06-03 add gamma - collides with motors
    [CanSat.iam, Hull_batt_pillar.ipt, gamma.ipt]
2018-06-03 pillar4 - nethole
    [Hull_batt_pillar4.ipt]
2018-06-03 Edit final version of pcbs, gerbers generated
    [arm-B.Cu.gbl, arm-B.Mask.gbs, arm-B.Paste.gbp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]
2018-06-04 nearly final
    [Arm.ipt, CanSat.iam, Hull_batt_pillar1.ipt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]
2018-06-10 Edit model - hull pillars edited to hold most components
    [Cam_antenna.ipt, CanSat.iam, Circuit.ipt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]
2018-06-10 Add presentation view of the model and edit hull_main
    [Arm.ipt, Batt_pillar.ipt, Cam_SD_base.ipt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]
2018-06-12 Edit model - add second camera position
    [CanSat.iam, Hull_batt_pillar2.ipt]
2018-06-13 Add analysis spreadsheat
    [Analysis.xlsx]
2018-06-19 Add printable schematics
    [CanSat-1.idw, CanSat.iam, CanSat.ipn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]
2018-06-21 Edit code - add some new libraries
    [CanSat-1.idw]
2018-06-23 Edit GPS interrupt handling
2018-06-27 Add files via upload
    Part of analysis focussed on atmospheric data.
    [Analysis part2.xlsx]
2018-06-28 Edit main code, add examples, fix spectroscopy
    [13725_Qwiic_Spectral_Sensor-AS726x-panel.v10.brd, AS726xBasicShroud.stl, AS726xProgrammerBase.stl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]
2018-06-29 Add data
    [Analysis1.xlsx]

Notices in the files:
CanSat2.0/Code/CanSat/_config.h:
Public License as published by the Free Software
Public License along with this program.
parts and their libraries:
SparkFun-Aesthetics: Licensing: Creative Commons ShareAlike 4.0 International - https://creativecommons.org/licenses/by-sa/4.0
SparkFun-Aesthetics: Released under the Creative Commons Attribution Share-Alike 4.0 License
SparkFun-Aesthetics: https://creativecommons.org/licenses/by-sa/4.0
